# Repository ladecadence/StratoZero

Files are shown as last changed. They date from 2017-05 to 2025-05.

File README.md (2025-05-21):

# StratoZero

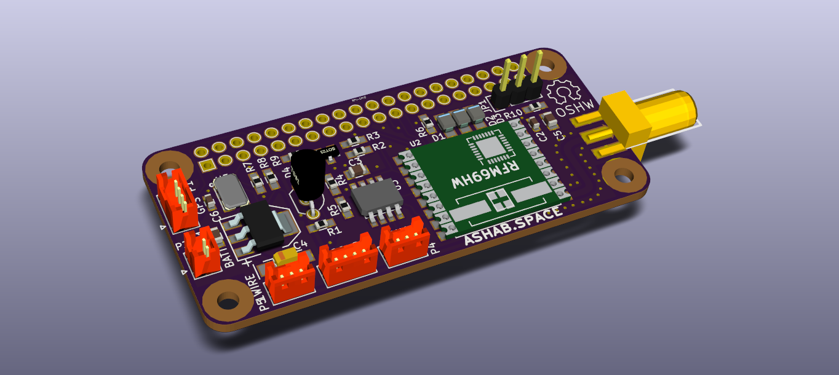
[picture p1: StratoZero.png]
StratoZero Board


StratoZero is a Raspberry Pi Zero hat for use in High Altitude Balloon missions.
It uses a RFM95 LoRa radio module, ds18b20 temperature sensors, a mcp3002 SPI ADC to monitor the battery, a MS5607 barometer, and several connectors for GPS, I2C, analog inputs, and more.

Check BOM File for components.

This board is designed to be used with the EkiGo flight software: [https://github.com/ladecadence/EkiGo](https://github.com/ladecadence/EkiGo)

## Component changes

 * Initial tests with the original voltage regulator showed brownouts, so now I'm using an MIC39100-5 and it works perfect (same footprint).
 * DS3231 and it's battery come from the small and cheap RTC modules you can find on ebay or aliexpress.

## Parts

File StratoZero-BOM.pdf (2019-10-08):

StratoZero

Page 1

Id Designator | Package | Designation | Supplier and ref
1 G*** | Banana | LOGO
2 C4 | TantalC_SizeA_EIA-3216_HandSoldering | CP
3 SMA_E1 | SMA_EDGE | SMA_EDGE
4 U2 | RFM95_SMD_Handsoldering | RFM95HW
5 C1 | C_0805 | 470n
6 C2,C6 | C_0603 | 100n
7 C3 | C_0805 | 100n
8 C5 | C_0805 | 1u
9 D1,D2,D3 | R_0805_HandSoldering | D
10 P6 | RPI-ZERO-Hat | RPI-GPIO
11 Q1 | SOT-23 | 2N7002
12 R1 | R_0603_HandSoldering | 4K7R
13 R2 | R_0603_HandSoldering | 100R
14 R3,R5,R6,R7,R8,R10 R_0603_HandSoldering | 10K
15 R4 | R_0603_HandSoldering | 22K
16 U1 | SOT-223 | LM2940
17 U3 | SOIC-8-N | MCP3002
18 U4 | TO-92_Inline_Wide | ds18b20
19 U5 | MS5607 | MS5607
20 | Symbol_OSHW-Logo_SilkScreen | Symbol_OSHW-Logo_SilkScreen
21 P1 | Hirose_DF13-04P-1.25DSA_04x1.25mm_Straight GPS
22 P2 | Hirose_DF13-04P-1.25DSA_04x1.25mm_Straight I2C
23 P3 | Hirose_DF13-02P-1.25DSA_02x1.25mm_Straight BATT
24 P4 | Hirose_DF13-03P-1.25DSA_03x1.25mm_Straight AN1
25 P5 | Hirose_DF13-03P-1.25DSA_03x1.25mm_Straight 1WIRE
26 G***,G*** | ASHAB-LOGO-FSILK | LOGO
27 D4 | LED_0603 | LED
28 R9 | R_0603_HandSoldering | 390R
29 JP1 | Pin_Header_Straight_1x03 | RF_PWR
30 P7 | Hirose_DF13-03P-1.25DSA_03x1.25mm_Straight GP1
31 U6 | SOIC-16W_7.5x10.3mm_P1.27mm | DS3231M
32 C7 | C_0603_1608Metric | 100n
33 BT1 | RTC-Batt | Battery_Cell

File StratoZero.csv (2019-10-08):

Id | Designator | Package | Quantity | Designation | Supplier and ref
1 | G*** | Banana | 1 | LOGO
2 | C4 | TantalC_SizeA_EIA-3216_HandSoldering | 1 | CP
3 | SMA_E1 | SMA_EDGE | 1 | SMA_EDGE
4 | U2 | RFM95_SMD_Handsoldering | 1 | RFM95HW
5 | C1 | C_0805 | 1 | 470n
6 | C2,C6 | C_0603 | 2 | 100n
7 | C3 | C_0805 | 1 | 100n
8 | C5 | C_0805 | 1 | 1u
9 | D1,D2,D3 | R_0805_HandSoldering | 3 | D
10 | P6 | RPI-ZERO-Hat | 1 | RPI-GPIO
11 | Q1 | SOT-23 | 1 | 2N7002
12 | R1 | R_0603_HandSoldering | 1 | 4K7R
13 | R2 | R_0603_HandSoldering | 1 | 100R
14 | R3,R5,R6,R7,R8,R10 | R_0603_HandSoldering | 6 | 10K
15 | R4 | R_0603_HandSoldering | 1 | 22K
16 | U1 | SOT-223 | 1 | LM2940
17 | U3 | SOIC-8-N | 1 | MCP3002
18 | U4 | TO-92_Inline_Wide | 1 | ds18b20
19 | U5 | MS5607 | 1 | MS5607
20 |  | Symbol_OSHW-Logo_SilkScreen | 1 | Symbol_OSHW-Logo_SilkScreen
21 | P1 | Hirose_DF13-04P-1.25DSA_04x1.25mm_Straight | 1 | GPS
22 | P2 | Hirose_DF13-04P-1.25DSA_04x1.25mm_Straight | 1 | I2C
23 | P3 | Hirose_DF13-02P-1.25DSA_02x1.25mm_Straight | 1 | BATT
24 | P4 | Hirose_DF13-03P-1.25DSA_03x1.25mm_Straight | 1 | AN1
25 | P5 | Hirose_DF13-03P-1.25DSA_03x1.25mm_Straight | 1 | 1WIRE
26 | G***,G*** | ASHAB-LOGO-FSILK | 2 | LOGO
27 | D4 | LED_0603 | 1 | LED
28 | R9 | R_0603_HandSoldering | 1 | 390
29 | JP1 | Pin_Header_Straight_1x03 | 1 | RF_PWR
30 | P7 | Hirose_DF13-03P-1.25DSA_03x1.25mm_Straight | 1 | GP1
31 | U6 | SOIC-16W_7.5x10.3mm_P1.27mm | 1 | DS3231M
32 | C7 | C_0603_1608Metric | 1 | 100n
33 | BT1 | RTC-Batt | 1 | Battery_Cell

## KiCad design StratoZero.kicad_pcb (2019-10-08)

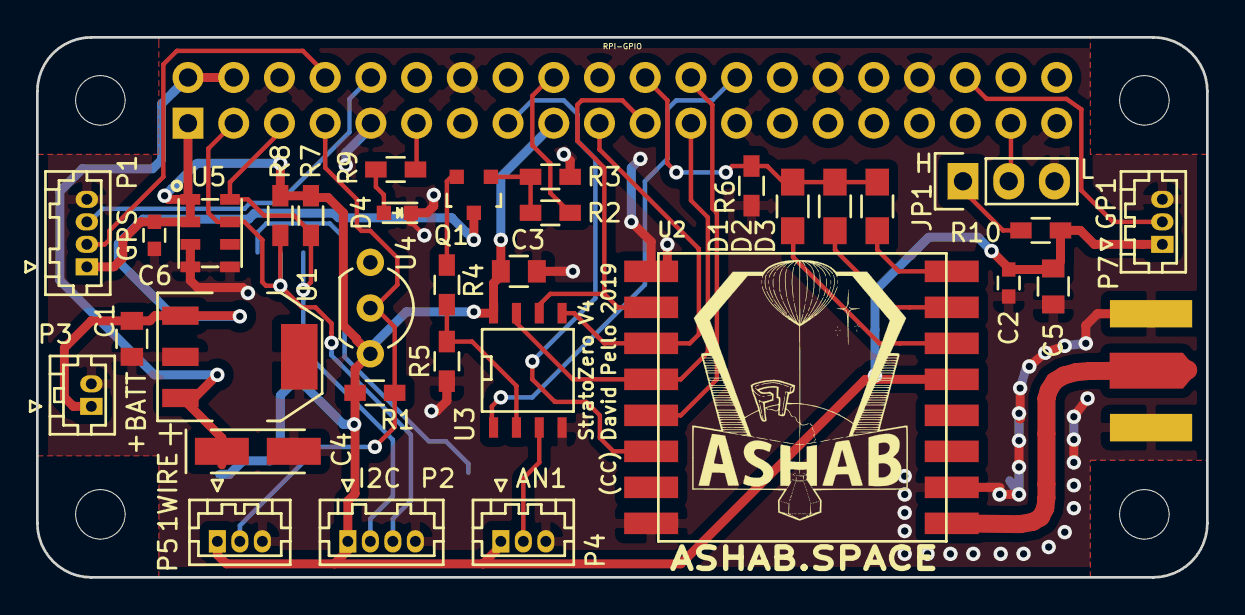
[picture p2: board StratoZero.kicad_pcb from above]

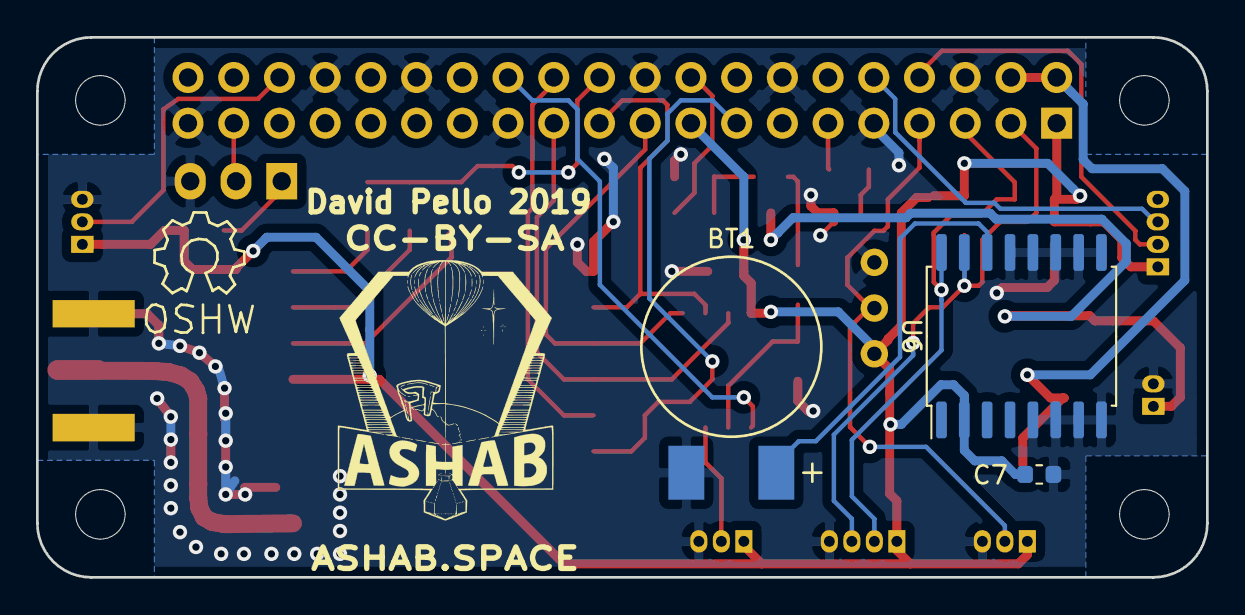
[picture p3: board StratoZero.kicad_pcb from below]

Board: 2 copper layers, 65.0 x 30.0 mm, 38 parts (3 on the bottom side), 31 nets.

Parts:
BT1: Battery_Cell; RTC-Batt
C1: 470n; C_0805
C2, C6: 100n; C_0603
C3: 100n; C_0805
C4: CP; TantalC_SizeA_EIA-3216_HandSoldering
C5: 1u; C_0805
C7: 100n; C_0603_1608Metric
D1, D2, D3: D; R_0805_HandSoldering
D4: LED; LED_0603
JP1: RF_PWR; Pin_Header_Straight_1x03
P1: GPS; Hirose_DF13-04P-1.25DSA_04x1.25mm_Straight
P2: I2C; Hirose_DF13-04P-1.25DSA_04x1.25mm_Straight
P3: BATT; Hirose_DF13-02P-1.25DSA_02x1.25mm_Straight
P4: AN1; Hirose_DF13-03P-1.25DSA_03x1.25mm_Straight
P5: 1WIRE; Hirose_DF13-03P-1.25DSA_03x1.25mm_Straight
P6: RPI-GPIO; RPI-ZERO-Hat
P7: GP1; Hirose_DF13-03P-1.25DSA_03x1.25mm_Straight
Q1: 2N7002; SOT-23
R1: 4K7R; R_0603_HandSoldering
R2: 100R; R_0603_HandSoldering
R3, R5, R6, R7, R8, R10: 10K; R_0603_HandSoldering
R4: 22K; R_0603_HandSoldering
R9: 390; R_0603_HandSoldering
SMA_E1: SMA_EDGE
U1: LM2940; SOT-223
U2: RFM95HW; RFM95_SMD_Handsoldering
U3: MCP3002; SOIC-8-N
U4: ds18b20; TO-92_Inline_Wide
U5: MS5607
U6: DS3231M; SOIC-16W_7.5x10.3mm_P1.27mm

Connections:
1WIRE: P5.2, P6.7, R1.2, U4.2
+3V3: C2.1, C3.1, C5.1, C6.1, C7.1, P1.1, P2.1, P4.1, P5.1, P6.1, P6.17, P7.1, R1.1, R7.1, R8.1, R10.2, U2.13, U3.8, U4.3, U5.1, U5.2, U6.2
+5V: C4.1, P6.2, P6.4, U1.3
+BATT: C1.1, P3.1, Q1.3, U1.1
/RF: SMA_E1.1, U2.9
AN1: P4.2, U3.3
CS0: P6.24, U2.5
CS1: P6.26, U3.1
EXT_GPIO: P6.36, P7.2
GND: BT1.2, C1.2, C2.2, C3.2, C4.2, C5.2, C6.2, C7.2, D4.1, JP1.3, P1.4, P2.4, P3.2, P4.3, P5.3, P6.6, P6.9, P6.14, P6.20, P6.25, P6.30, P6.34, P6.39, P7.3, R3.2, R5.2, R6.2, SMA_E1.0, SMA_E1.2, U1.2, U1.4, U2.1, U2.8, U2.10, U3.4, U4.1, U5.3, U5.4, U5.5, U6.5, U6.6, U6.7, U6.8, U6.9, U6.10, U6.11, U6.12, U6.13
LED: P6.11, R9.2
LORA_INT: D1.1, D2.1, D3.1, P6.22, R6.1
LORA_RST: P6.15, U2.6
MISO: P6.21, U2.2, U3.6
MOSI: P6.19, U2.3, U3.5
unnamed: D1.2, U2.14
unnamed: D2.2, U2.15
unnamed: D3.2, U2.16
unnamed: D4.2, R9.1
unnamed: JP1.1, R10.1
unnamed: Q1.1, R2.1, R3.1
unnamed: Q1.2, R4.1
unnamed: R4.2, R5.1, U3.2
READ_BATT_EN: P6.18, R2.2
RXD: P1.3, P6.10
SCL: P2.2, P6.5, R7.2, U5.8, U6.16
SCLK: P6.23, U2.4, U3.7
SDA: P2.3, P6.3, R8.2, U5.7, U6.15
TXD: P1.2, P6.8
TX_PWR: JP1.2, P6.37
VMEM: BT1.1, U6.14

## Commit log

2017-05-15 initial import, v0.2, RF power jumper
    [StratoZero.kicad_pcb, StratoZero.sch]
2017-05-26 Improved RF Path
    [StratoZero.kicad_pcb]
2019-10-08 Updated to V4, minor fixes and new RTC and battery on board
    [StratoZero.csv, StratoZero.kicad_pcb, StratoZero.sch]

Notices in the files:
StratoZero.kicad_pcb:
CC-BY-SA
